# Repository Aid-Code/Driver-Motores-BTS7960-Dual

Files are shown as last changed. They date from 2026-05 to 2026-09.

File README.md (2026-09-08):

# TitanCore 7960: Driver BTS7960 Dual Channel Custom
#### Buenas! Soy Aiden, y les quise escribir un pequeño texto para comentarles de este desarrollo que hice para mi robot y para la comunidad!

## Origen
La idea inicialmente empezó porque utilizaba un Monster Shield (VNH2SP30) que no suele ser tan fácil de conseguir, y quizás si se consigue es caro, por lo que necesitaba conseguir una alternativa a este driver de motores para mi robot Sumo.  
De ahí empecé a buscar como funcionaba un **Puente H**, que componentes se usaban, que transistores usar y por qué.   
Como primer acercamiento armé un Puente H con transistores mosfet en una placa experimental, usando gate drivers, que milagrosamente funcionó (después de revisar 50 veces mis dudosas soldaduras a las 5 A.M), pero cuando hice un primer diseño de la PCB, me di cuenta que no era lo suficientemente eficiente en espacio.
No importaba cuantos componentes SMD usara, era imposible reducirla.   
Más adelante, después de un tiempo de buscar (y charlar con mi LLM de confianza) encontré que existían encapsulados que integraban dos transistores "en uno". 
A todo esto, yo ya conocía el módulo comercial del BTS7960, pero me parecía una placa gigante (con un disipador gigante) para el uso que yo le quería dar. En esta parte de mi investigación descubrí que los BTS7960 eran esos peculiares encapsulados que integraban "dos transistores en uno". Por lo que dije PERFECTO, LOS COMPRO; LOS DESUELDO; ARMO MI PLACA!  
Dicho y hecho, acá estamos!

## Funcionamiento
La dinamica de este driver de motores es un poco distinta a lo habitual, comparandola con un Monster Shield o un L298n.  
Los pines son:
- GND
- VCC --> Voltaje lógico de 3.3v a 5v
- EN_1 --> Habilita el paso de corriente al Canal 1 (Opcional conectarlo a un pin, puede ir a VCC)
- EN_2 --> Habilita el paso de corriente al Canal 2 (Opcional conectarlo a un pin, puede ir a VCC)
- PWM_A --> Señal PWM del Canal 1 en una dirección
- PWM_B --> Señal PWM del Canal 1 en dirección contraria
- PWM_C --> Señal PWM del Canal 2 en una dirección
- PWM_D --> Señal PWM del Canal 2 en dirección contraria

- VS --> Voltaje de alimentación y salida a los motores de 6v a 28v (**Aprox. basado en la datasheet del BTS7960**)

## Puesto a prueba
Hasta ahora los parametros con los que puse a prueba el funcionamiento del driver son:  
- VCC: 5v
- VS: ~15v

La idea es utilizarlo a 24v con motores que podrían llegar a consumir 11,2A por canal. Cuando lo pruebe y confirme que no explota lo comento!

## Licencia y Uso Comercial
*Este proyecto está licenciado bajo* **Creative Commons Atribución-NoComercial-CompartirIgual 4.0 Internacional (CC BY-NC-SA 4.0)**. Consulta el archivo [LICENSE](LICENSE) para más detalles.
- *Puedes clonar, fabricar, estudiar y modificar este diseño libremente para proyectos personales, educativos o de competencia.*
- *Queda terminantemente prohibida la comercialización, venta directa o integración comercial de este diseño sin autorización previa.*
- Para consultas comerciales o adquisición de módulos ensamblados, contactar a: aiden.maidp@gmail.com

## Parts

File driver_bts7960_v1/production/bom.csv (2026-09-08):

Designator | Footprint | Quantity | Value | LCSC Part #
C1, C2, C3, C4 | 0805 | 4 | 100nF
C5 | CP_Radial_D8.0mm_P5.00mm | 1 | 330uF
J1 | AMASS_XT30U-F_1x02_P5.0mm_Vertical | 1 | Motor_1
J2 | AMASS_XT30U-F_1x02_P5.0mm_Vertical | 1 | XT30
J3 | PinHeader_1x08_P2.54mm_Vertical | 1 | Conn_01x08_Pin
J6 | AMASS_XT30U-F_1x02_P5.0mm_Vertical | 1 | Motor_2
R1, R10, R2, R3, R4, R5, R6, R7, R8, R9 | 0805 | 10 | 10k
R11, R12, R13, R14 | 0805 | 4 | 30k
U1, U2, U3, U4 | BTS7960B_DPAK127P1490X440-8N | 4 | BTS7960B
U5 | SOIC127P1032X265-20N | 1 | 74HC244

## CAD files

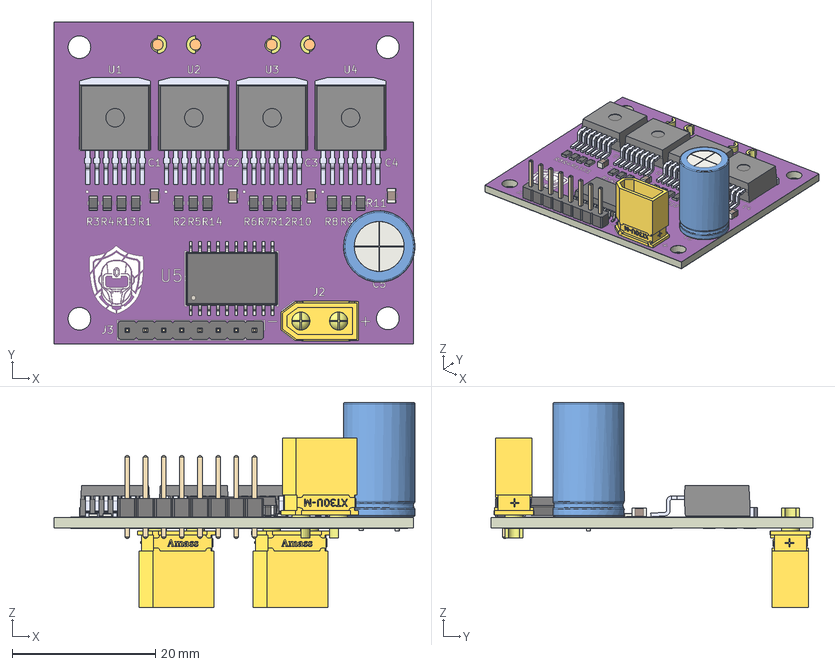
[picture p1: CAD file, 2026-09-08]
titancore_7960.step
50.5 x 45.0 x 28.7 mm
R_0805_2012Metric x 14
PinHeader_1x08_P2.54mm_Vertical
C_0805_2012Metric x 4
BTS7960B x 4
XT30 Male x 3
SOIC-20W_7.5x12.8mm_P1.27mm
C_Radial_D10.0mm_H16.0mm_P5.00mm
driver_bts7960_v1_copper
driver_bts7960_v1_via
driver_bts7960_v1_silkscreen x 2
driver_bts7960_v1_soldermask x 2
driver_bts7960_v1_PCB

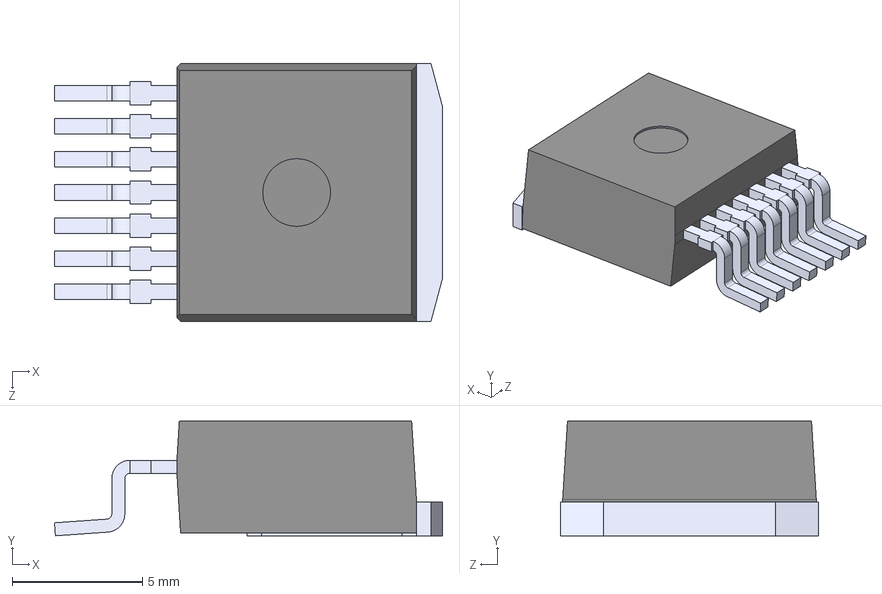
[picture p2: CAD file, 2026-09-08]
BTS7960B.step
14.9 x 4.40 x 9.90 mm

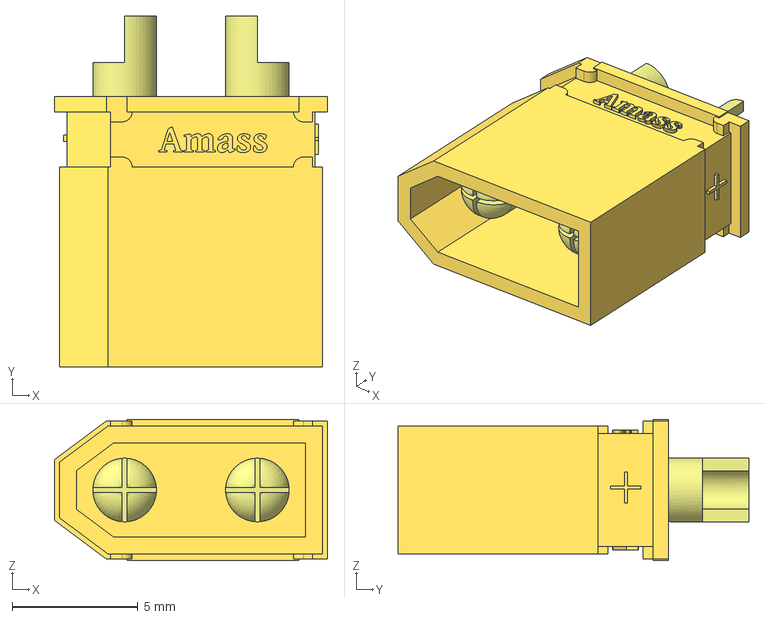
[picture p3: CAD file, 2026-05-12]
XT30 Male.stp
10.9 x 14.0 x 5.62 mm

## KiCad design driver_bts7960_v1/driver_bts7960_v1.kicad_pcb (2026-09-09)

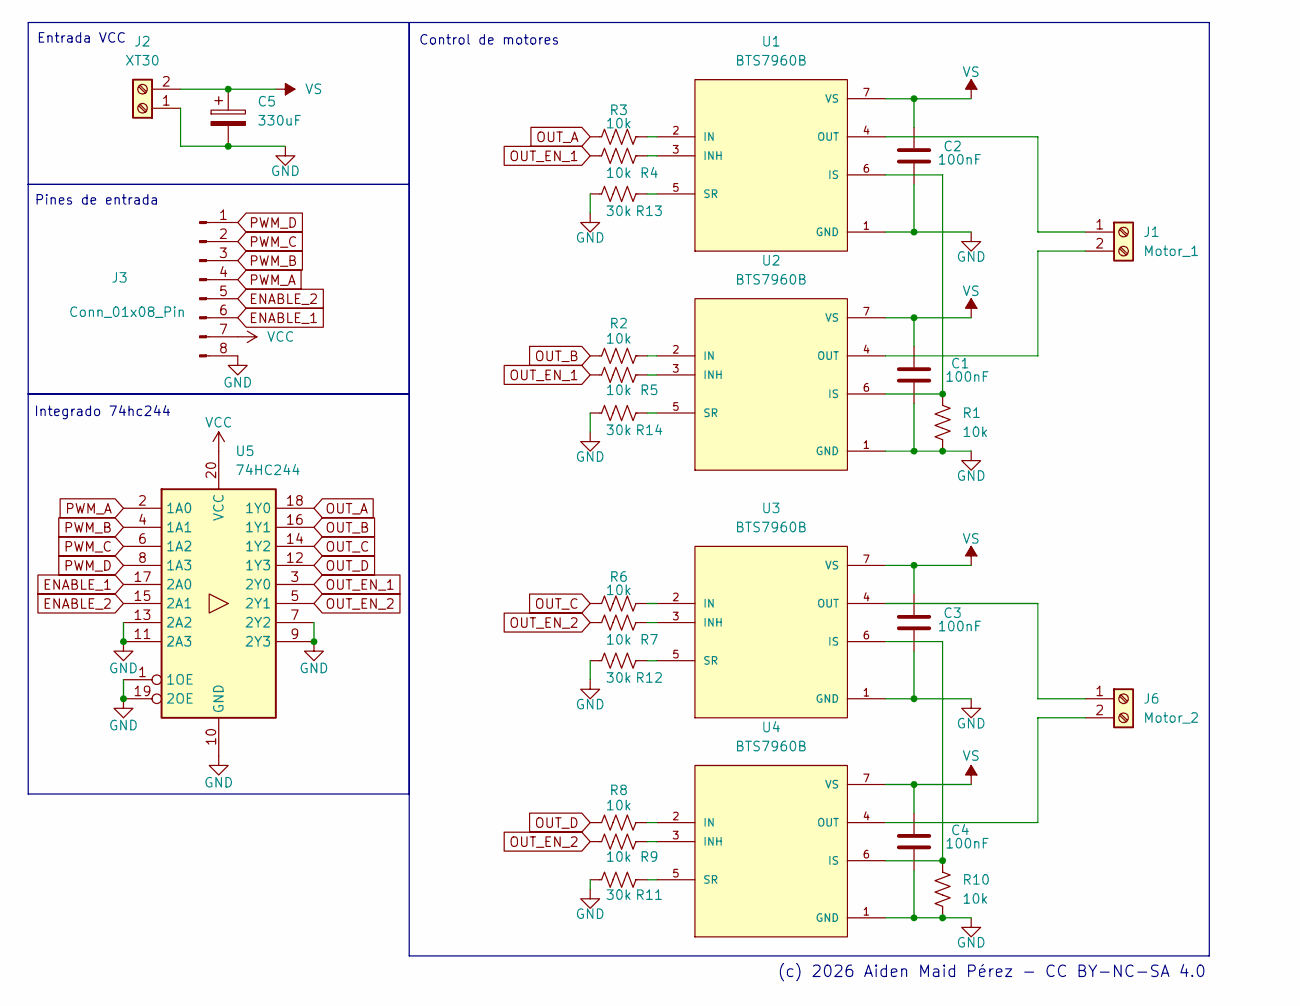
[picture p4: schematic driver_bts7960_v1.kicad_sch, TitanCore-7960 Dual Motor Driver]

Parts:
C1, C2, C3, C4: 100nF; C_0805_2012Metric_Pad1.18x1.45mm_HandSolder
C5: 330uF; CP_Radial_D8.0mm_P5.00mm
J1: Motor_1; AMASS_XT30U-F_1x02_P5.0mm_Vertical
J2: XT30; AMASS_XT30U-F_1x02_P5.0mm_Vertical
J3: Conn_01x08_Pin; PinHeader_1x08_P2.54mm_Vertical
J6: Motor_2; AMASS_XT30U-F_1x02_P5.0mm_Vertical
R1, R2, R3, R4, R5, R6, R7, R8, R9, R10: 10k; R_0805_2012Metric_Pad1.20x1.40mm_HandSolder
R11, R12, R13, R14: 30k; R_0805_2012Metric_Pad1.20x1.40mm_HandSolder
U1, U2, U3, U4: BTS7960B; BTS7960B_DPAK127P1490X440-8N; PARTREV 1.1
U5: 74HC244; SOIC127P1032X265-20N

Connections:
ENABLE_1: J3.6, U5.17 (2A0)
ENABLE_2: J3.5, U5.15 (2A1)
GND: C1.2, C2.2, C3.2, C4.2, C5.2, J2.1, J3.8, R1.2, R10.2, R11.2, R12.2, R13.2, R14.2, U1.1 (GND), U2.1 (GND), U3.1 (GND), U4.1 (GND), U5.1 (1OE), U5.7 (2Y2), U5.9 (2Y3), U5.10 (GND), U5.11 (2A3), U5.13 (2A2), U5.19 (2OE)
unnamed: J1.1, U1.4 (OUT), U1.8 (OUT)
unnamed: J1.2, U2.4 (OUT), U2.8 (OUT)
unnamed: J6.1, U3.4 (OUT), U3.8 (OUT)
unnamed: J6.2, U4.4 (OUT), U4.8 (OUT)
unnamed: R3.1, U1.2 (IN)
unnamed: R4.1, U1.3 (INH)
unnamed: R1.1, U1.6 (IS), U2.6 (IS)
unnamed: R13.1, U1.5 (SR)
unnamed: R2.1, U2.2 (IN)
unnamed: R5.1, U2.3 (INH)
unnamed: R14.1, U2.5 (SR)
unnamed: R6.1, U3.2 (IN)
unnamed: R7.1, U3.3 (INH)
unnamed: R10.1, U3.6 (IS), U4.6 (IS)
unnamed: R12.1, U3.5 (SR)
unnamed: R8.1, U4.2 (IN)
unnamed: R9.1, U4.3 (INH)
unnamed: R11.1, U4.5 (SR)
OUT_A: R3.2, U5.18 (1Y0)
OUT_B: R2.2, U5.16 (1Y1)
OUT_C: R6.2, U5.14 (1Y2)
OUT_D: R8.2, U5.12 (1Y3)
OUT_EN_1: R4.2, R5.2, U5.3 (2Y0)
OUT_EN_2: R7.2, R9.2, U5.5 (2Y1)
PWM_A: J3.4, U5.2 (1A0)
PWM_B: J3.3, U5.4 (1A1)
PWM_C: J3.2, U5.6 (1A2)
PWM_D: J3.1, U5.8 (1A3)
VCC: J3.7, U5.20 (VCC)
VS: C1.1, C2.1, C3.1, C4.1, C5.1, J2.2, U1.7 (VS), U2.7 (VS), U3.7 (VS), U4.7 (VS)

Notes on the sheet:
Entrada VCC
Pines de entrada
Integrado 74hc244
Control de motores
(c) 2026 Aiden Maid Pérez - CC BY-NC-SA 4.0

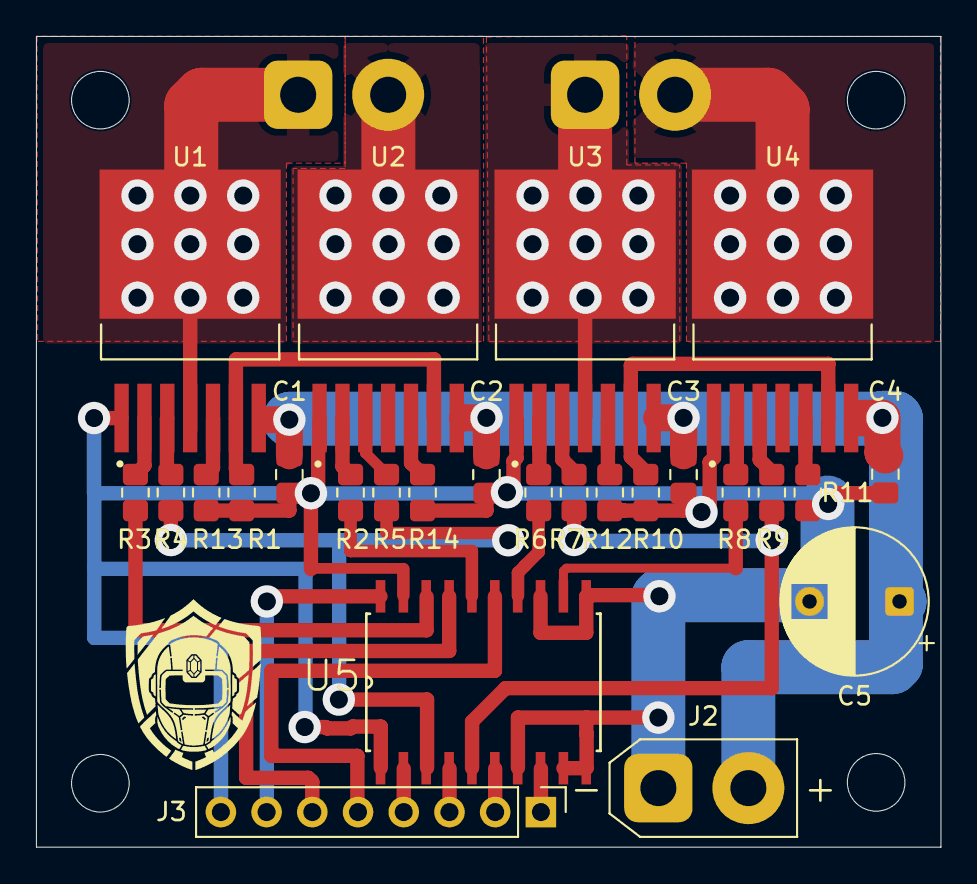
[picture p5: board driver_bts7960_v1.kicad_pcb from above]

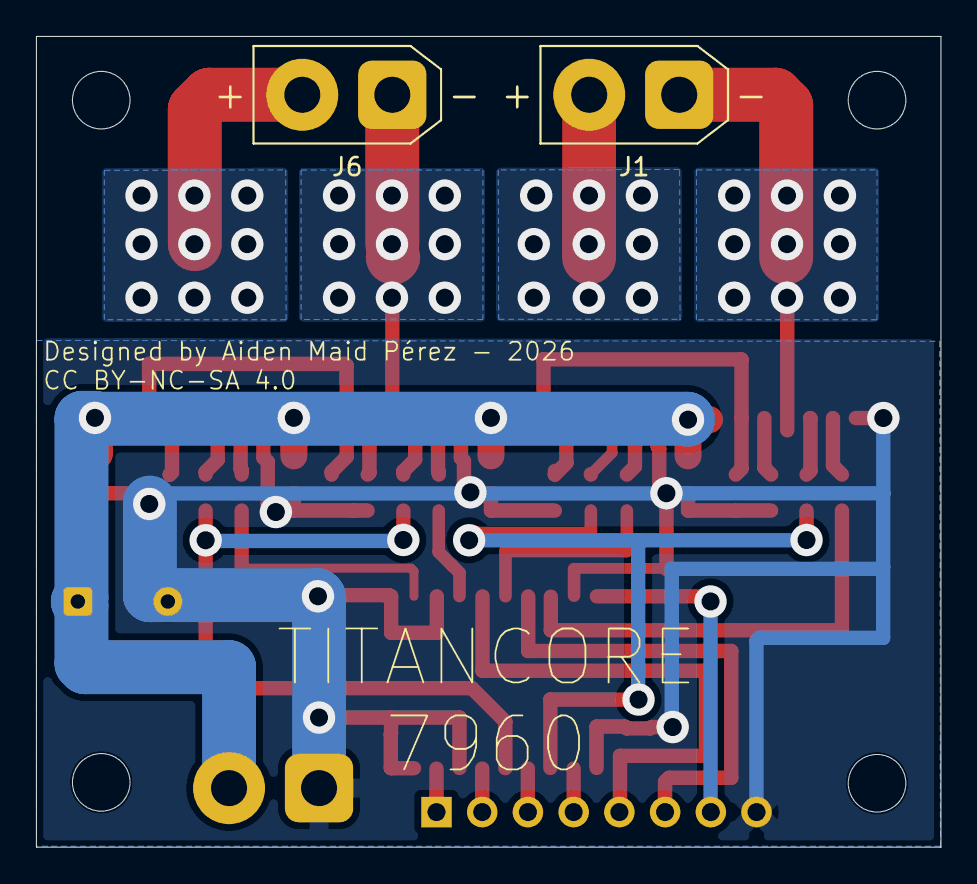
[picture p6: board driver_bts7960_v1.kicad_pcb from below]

Board: 2 copper layers, 50.3 x 45.0 mm, 28 parts (2 on the bottom side), 33 nets.

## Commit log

2025-12-22 driver v1
    [driver_bts7960.kicad_pcb, driver_bts7960.kicad_sch]
2025-12-22 driver bts7960 v1
    [driver_bts7960.kicad_pcb, driver_bts7960_v1.kicad_pcb, driver_bts7960_v1.kicad_sch]
2025-12-23 driver bts7960 v2
    [driver_bts7960_v1.kicad_pcb, driver_bts7960_v2.kicad_pcb, driver_bts7960_v2.kicad_sch]
2026-05-12 v2 terminado con 74hc244
    [BTS7960B.SLDPRT, XT30 Male.stp, driver_bts7960_v1.kicad_pcb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]
2026-06-06 footprint 74hc244 corregido
    [driver_bts7960_v1.kicad_pcb, driver_bts7960_v1.kicad_sch]

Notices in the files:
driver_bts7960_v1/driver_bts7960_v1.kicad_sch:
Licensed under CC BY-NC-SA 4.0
